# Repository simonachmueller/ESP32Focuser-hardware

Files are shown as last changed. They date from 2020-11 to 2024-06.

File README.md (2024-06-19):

# ESP32Focuser Hardware
This is a repository for storing documentation for my [ESP32Focuser](https://github.com/simonachmueller/ESP32Focuser) project.

Описание на русском

Deutsche Beschreibung

# What is that about
Focuser for astronomy telescope based on ESP32 controller. Comportable with Indilib (http:/indilib.org/) and ASCOM (https://ascom-standards.org/).
The controller uses the protocol Moonlite (as documented in the indilib project).

# What hardware do I need
The firmware runs on a [ESP32-DevKitC](https://www.espressif.com/en/products/devkits/esp32-devkitc/overview) board. It uses also the [BIGTREETECH TMC2209 V1.2 Stepper Motor Driver](https://github.com/bigtreetech/BIGTREETECH-TMC2209-V1.2) to drive the motor on a super-silent and vibrationless way. Basically, you only need this two boards to start using the focuser. If you want to build it on a more resilient way, you can follow intructions below.

# Schematics
Schematics diagram can be found as a KiCad project [folder](/schematics). You can donwload shematics as pdf [here](/schematics/ESP32Focuser.sch.pdf).

The schematics is pretty easy. You just connect the pins of the ESP32 dev board with the TMC2209 board, add power supply and connect motor - from this point you can control the focuser from the computer over ASCOM/INDI driver. If you want to use an optical encoder as a handcontroller (what I would really advise you if you want to get rid of vibrations when you touch the telescope focuser knob), connect it to the pins on the ESP32 board as well.

## Wiring table
Please use the wiring table as reference, it might get outdated. For the most latest schematics version, check the KiCad project.

| Description | ESP32 board | TMC2209 board | Note |
| --- | --- | --- | ---- |
| DIR | 32 | DIR | |
| STEP | 33 | STEP | |
| CLK | 25 | CLK | |
| PDN | 26 | PDN + PDN | not used |
| MS2 | 14 | MS2 | |
| MS1 | 12 | MS1 | |
| EN | 13 | EN | |
| ENC1 | 2 | | Encoder output 1 |
| ENC2 | 15 | | Encoder output 2 |
| 5V | 5V | VDD | |
| 12V | | VM | Motor power supply |

## Stepper motor
I use the 17HS2408 stepper motor, as it fits well for 12v supply: it has 8 Ohm phase resistance what leads to 1.5 Amps phase current, it's a bit over the specification (rated current 0.6 Amps) but as it's not supposed to continuously work on high speed in this project,it works just fine, has enough torque and does smooth movements. 

## BOM
Aka bill of material

| Description | AliExpress link |  Notes |
| --- | --- | --- |
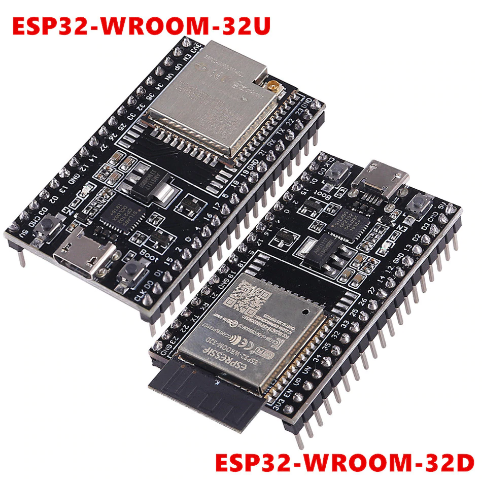
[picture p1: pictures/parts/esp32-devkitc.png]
| ESP32-DevKitC | https://www.aliexpress.com/item/4000103411061.html |  |
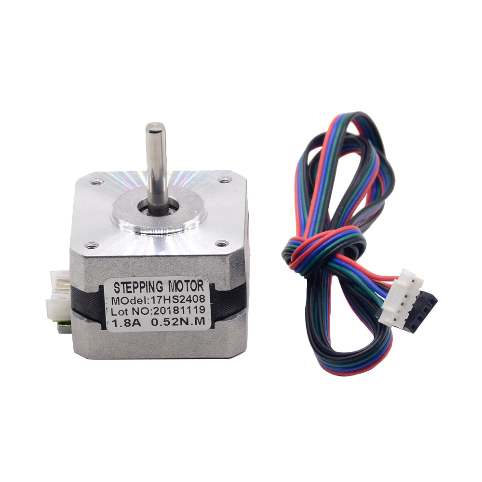
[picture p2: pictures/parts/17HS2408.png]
| 17HS2408 stepper motor | https://www.aliexpress.com/item/33033986185.html |  |
| 7 M3 screws for motor and encoder  | https://www.aliexpress.com/item/32965979997.html | M3 50pcs + 5mm  |
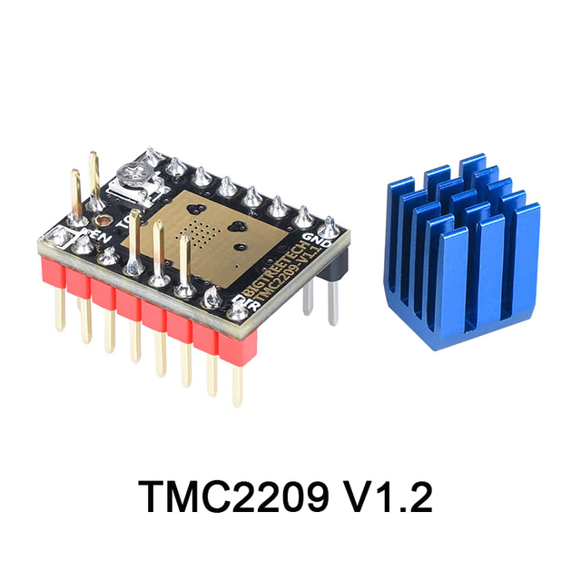
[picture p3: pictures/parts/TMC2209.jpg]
| TMC2209 board | https://www.aliexpress.com/item/33029587820.html |  |
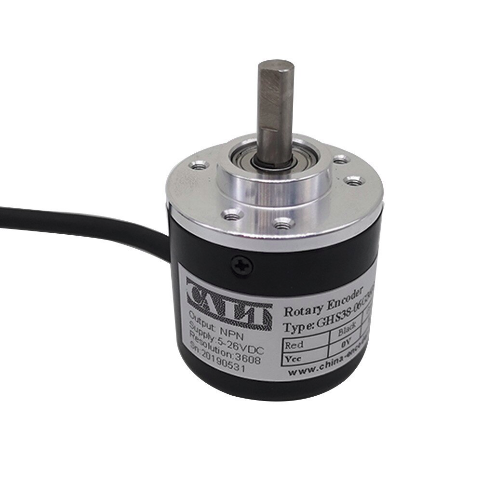
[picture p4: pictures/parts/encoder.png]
| Optical rotary encoder CALT ES38 | https://www.aliexpress.com/item/33028641351.html | 5v 600ppr  |
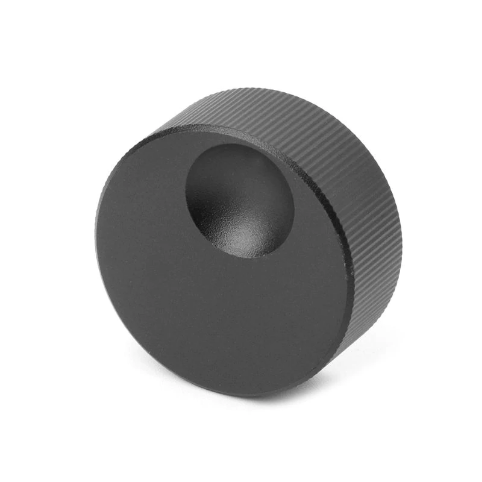
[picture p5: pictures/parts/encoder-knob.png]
| 13x32mm Encoder knob | https://www.aliexpress.com/item/33039964137.html | |
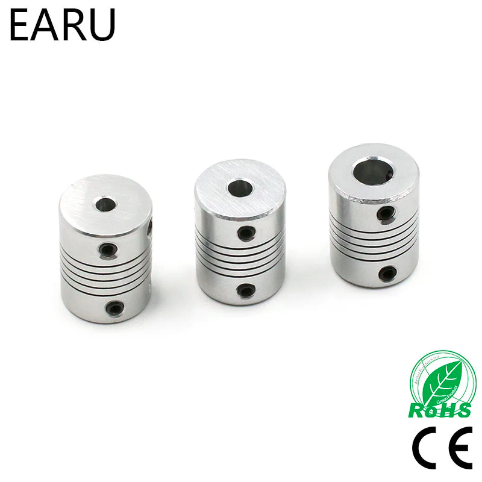
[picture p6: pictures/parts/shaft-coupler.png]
| Motor shaft coupler 5mm x ?? mm| https://www.aliexpress.com/item/32913158582.html ||
| OR alternatively to the direct coupling your motor with the focuser, you could use a belt like this below|||
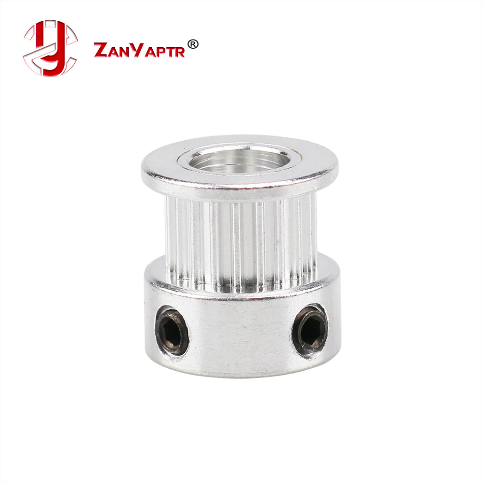
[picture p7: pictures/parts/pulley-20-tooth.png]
| GT2 Pulley 20 tooth ø 5mm| https://www.aliexpress.com/item/32724156349.html ||
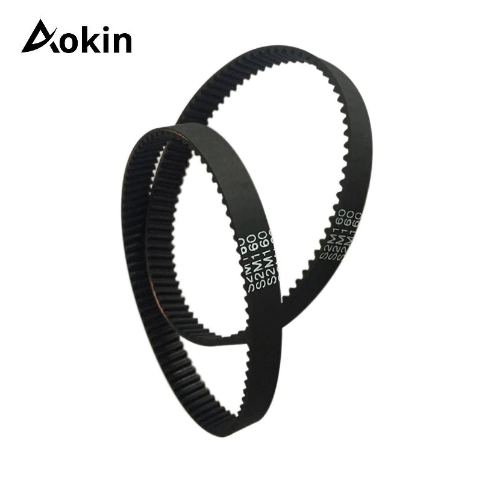
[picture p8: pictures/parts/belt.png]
| GT2 Closed Loop Timing Belt | https://www.aliexpress.com/item/32950422029.html ||
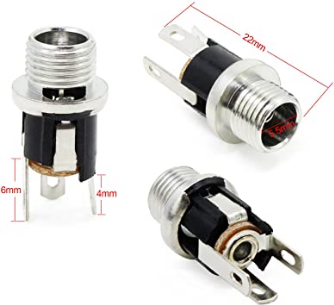
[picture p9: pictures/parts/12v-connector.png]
| 12v female plug 5.5mm x 2.1mm | |  |
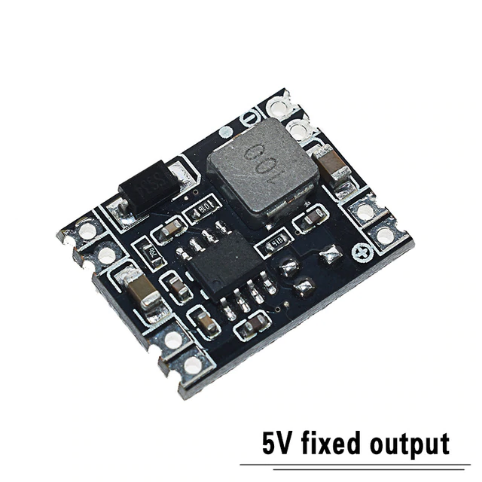
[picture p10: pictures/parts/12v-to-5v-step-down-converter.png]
| 12v→5v DC-DC step down converter board| https://www.aliexpress.com/item/32742116421.html ||
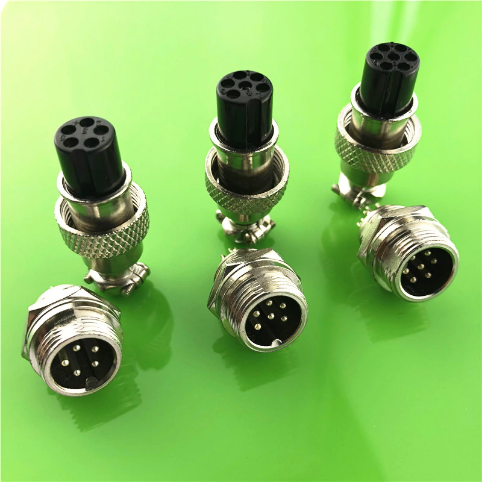
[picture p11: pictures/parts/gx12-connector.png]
| Hand controller connector M GX12 5 pin for encoder | https://www.aliexpress.com/item/32869491577.html | |
| Hand controller connector M GX12 4 pin for motor | https://www.aliexpress.com/item/32869491577.html | |
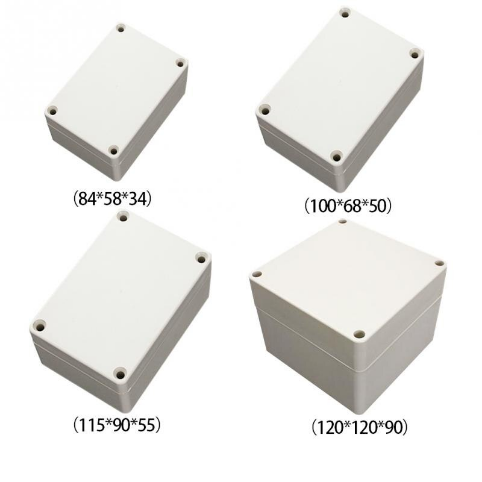
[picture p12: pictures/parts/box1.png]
| 115 90 55mm plastic enclosure case | https://www.aliexpress.com/item/32709832386.html |  |
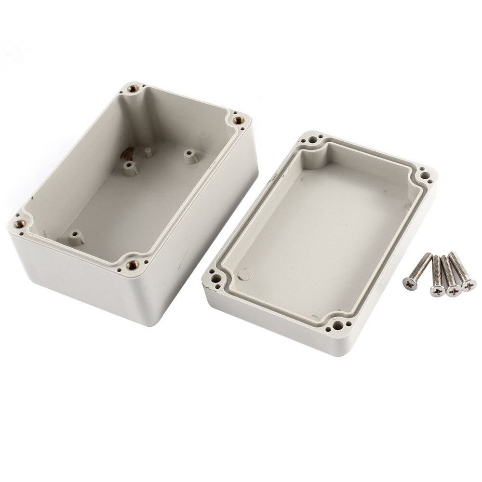
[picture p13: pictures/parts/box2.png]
| 100x68x50mm plastic enclosure case for encoder | https://www.aliexpress.com/item/32792270384.html | |
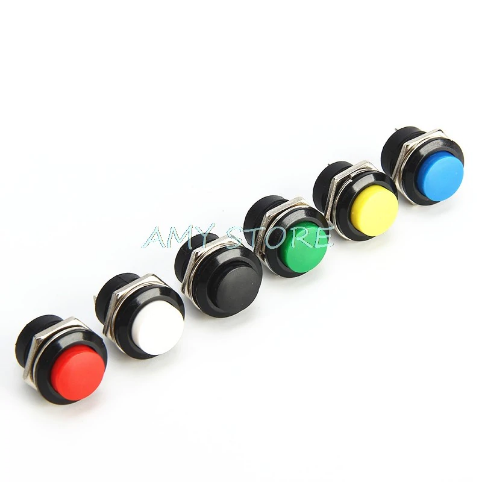
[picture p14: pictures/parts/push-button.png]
| Push button for handcontroller | https://www.aliexpress.com/item/32965284265.html ||
| Micro USB cable | tbd | |
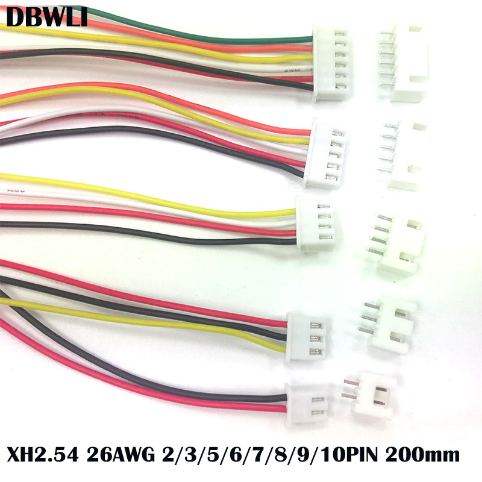
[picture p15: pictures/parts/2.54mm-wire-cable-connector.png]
| 2.54mm Wire Cable Connector 4 pin | https://www.aliexpress.com/item/32954418743.html | |
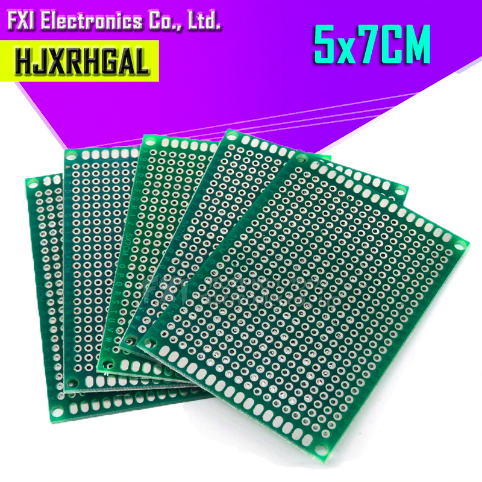
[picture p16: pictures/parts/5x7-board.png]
| Prototyping board 5x7 cm | https://www.aliexpress.com/item/32853911495.html |  |
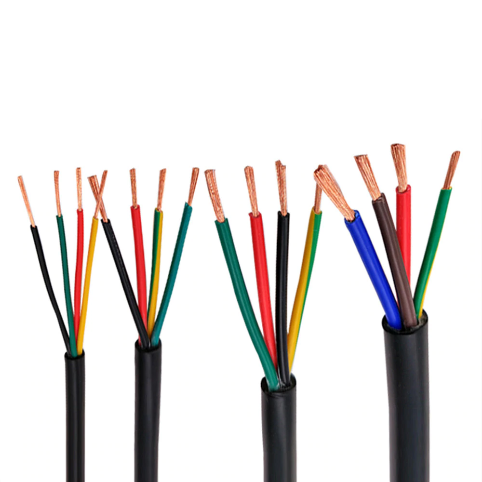
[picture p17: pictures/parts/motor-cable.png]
| Cable for motor 4 cores 0.3mm 22awg | https://www.aliexpress.com/item/4000714461664.html | |

# Pictures

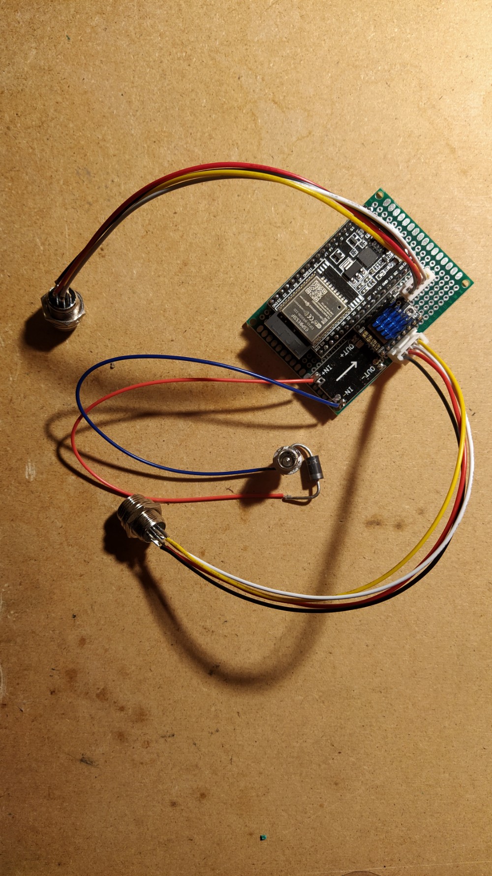
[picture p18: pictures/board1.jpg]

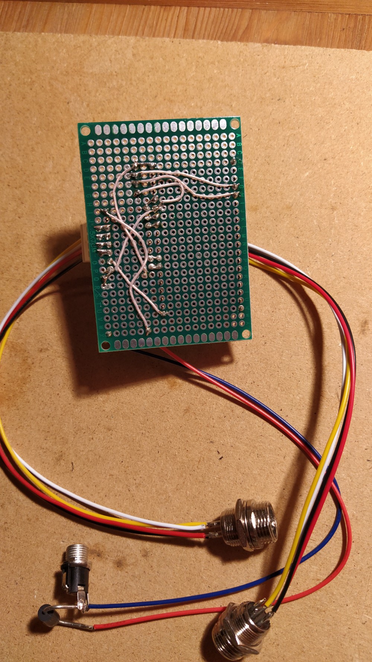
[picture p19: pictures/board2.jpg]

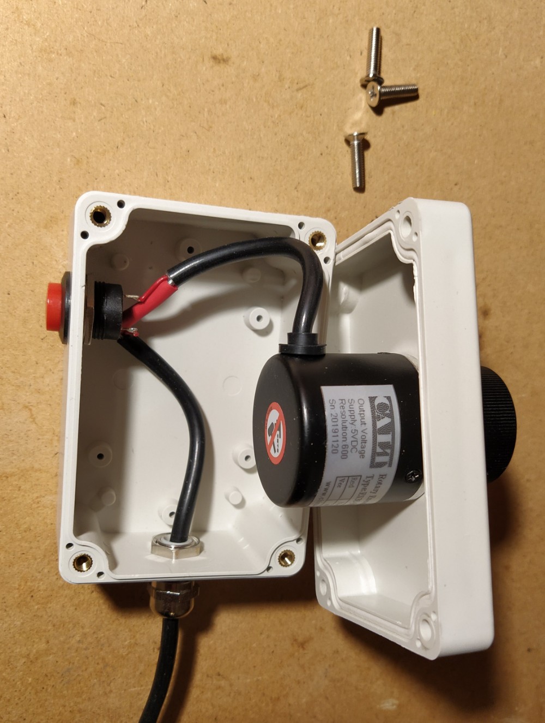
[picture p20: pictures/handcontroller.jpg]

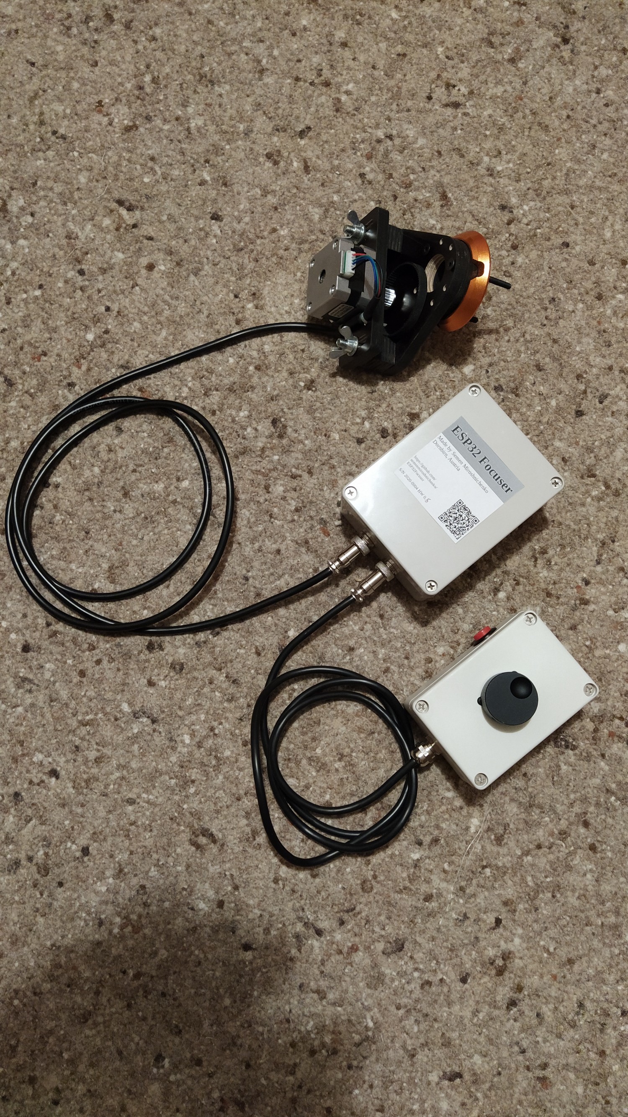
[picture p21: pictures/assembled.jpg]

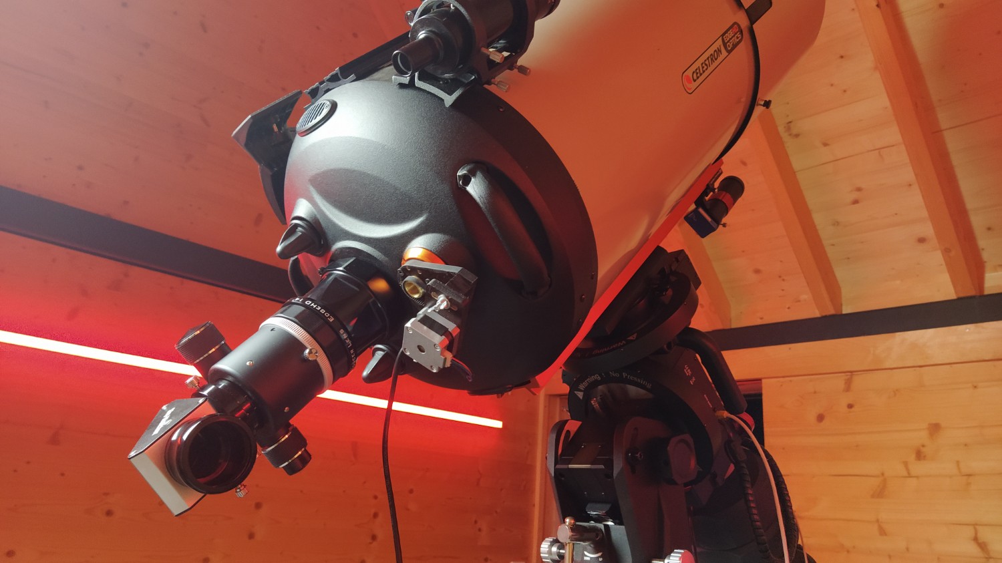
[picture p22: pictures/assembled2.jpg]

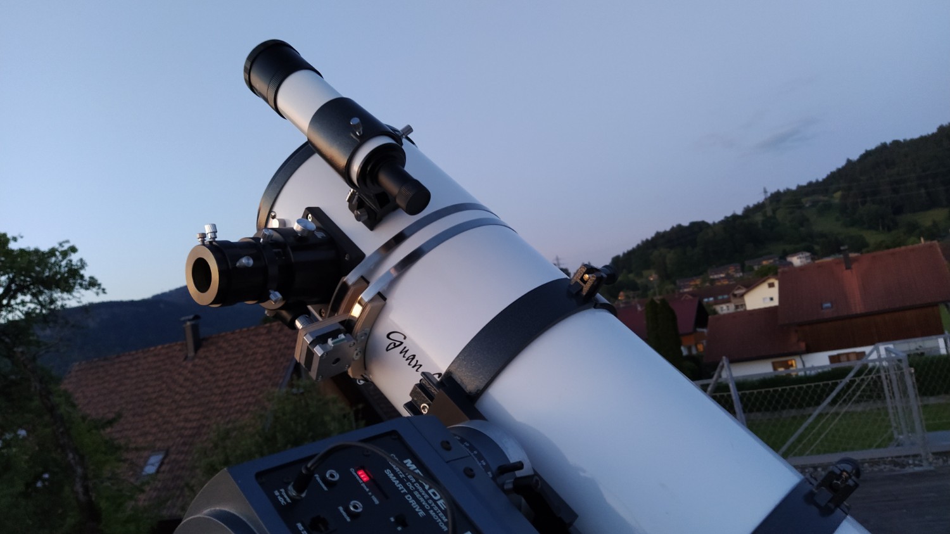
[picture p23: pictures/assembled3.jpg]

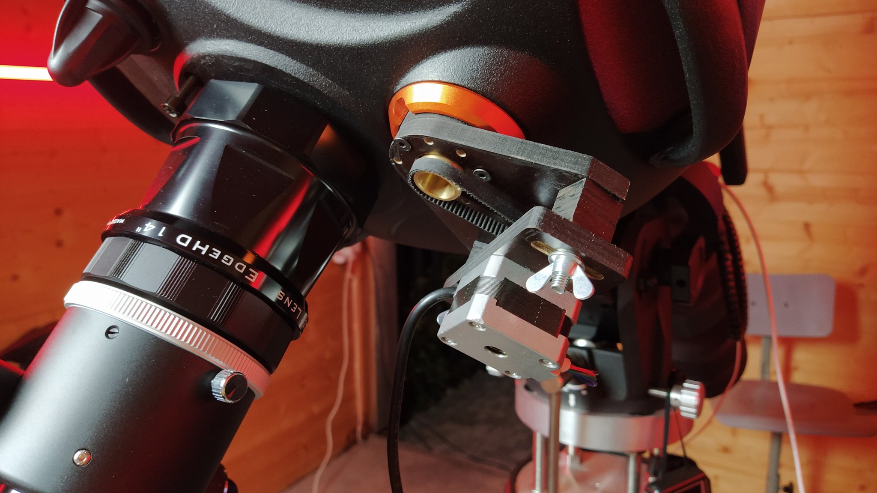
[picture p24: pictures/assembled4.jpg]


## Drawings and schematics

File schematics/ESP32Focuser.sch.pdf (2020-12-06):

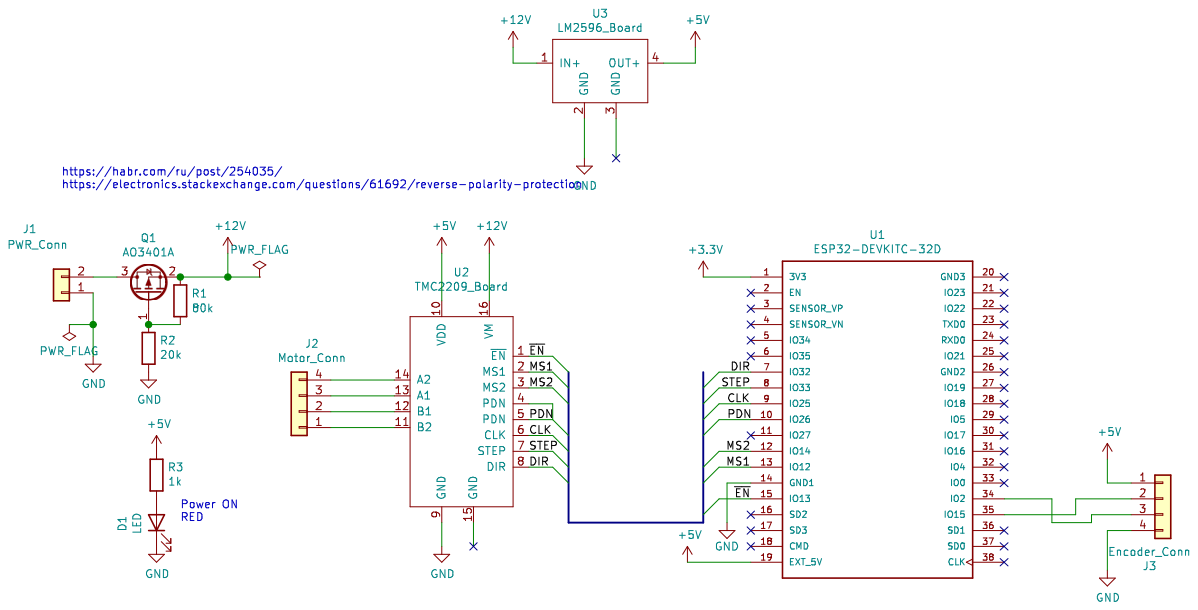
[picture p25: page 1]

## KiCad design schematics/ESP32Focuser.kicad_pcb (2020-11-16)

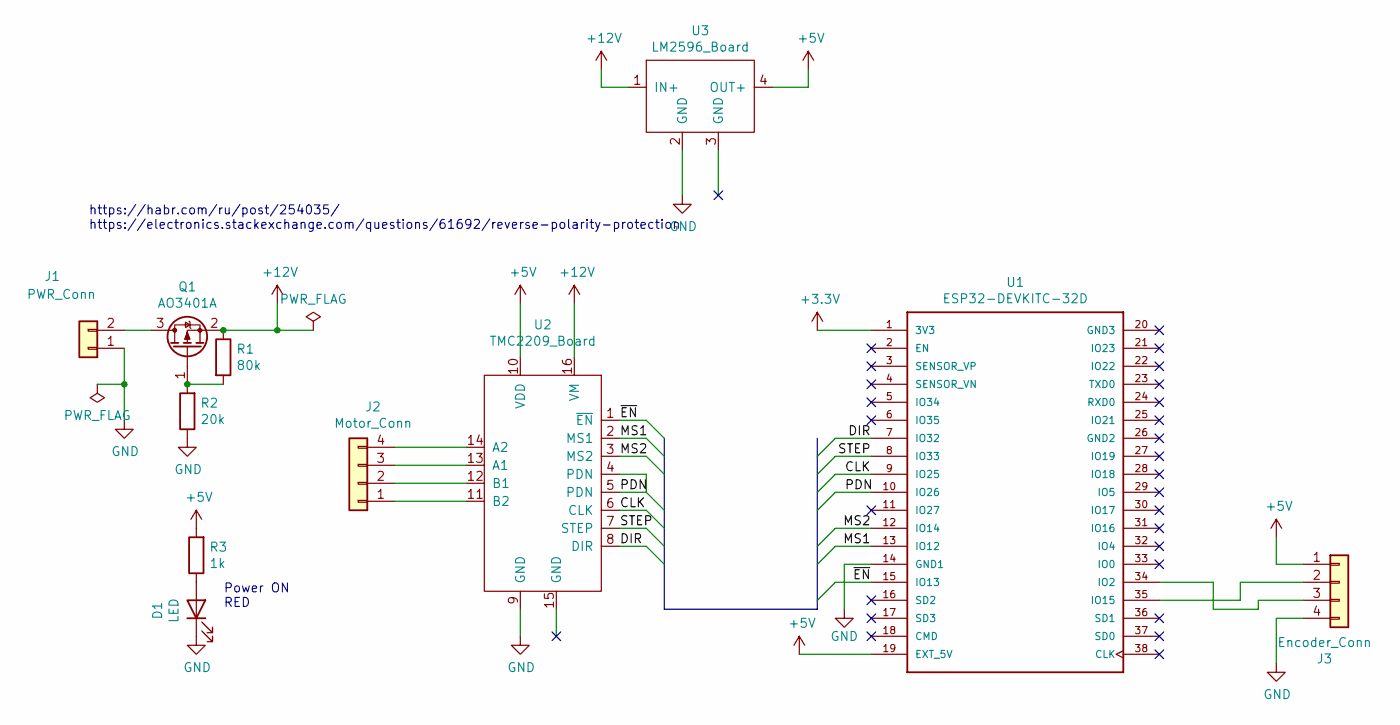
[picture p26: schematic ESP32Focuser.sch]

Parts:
D1: LED; LED_D3.0mm
J1: PWR_Conn; PinSocket_1x02_P2.54mm_Vertical
J2: Motor_Conn; PinSocket_1x04_P2.54mm_Vertical
J3: Encoder_Conn; PinSocket_1x04_P2.54mm_Vertical
Q1: AO3401A; SOT-23
R1: 80k; R_0805_2012Metric_Pad1.15x1.40mm_HandSolder
R2: 20k; R_0805_2012Metric_Pad1.15x1.40mm_HandSolder
R3: 1k; R_0805_2012Metric_Pad1.15x1.40mm_HandSolder
U1: ESP32-DEVKITC-32D; MODULE_ESP32-DEVKITC-32D
U2: TMC2209_Board; TMC2209_Module
U3: LM2596_Board; LM2596_Module

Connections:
+3V3: U1.1 (3V3)
+5V: J3.1, R3.2, U1.19 (EXT_5V), U2.10 (VDD), U3.4 (OUT+)
+12V: Q1.2 (S), R1.1, U2.16 (VM), U3.1 (IN+)
/CLK: U1.9 (IO25), U2.6 (CLK)
/DIR: U1.7 (IO32), U2.8 (DIR)
/MS1: U1.13 (IO12), U2.2 (MS1)
/MS2: U1.12 (IO14), U2.3 (MS2)
/PDN: U1.10 (IO26), U2.4 (PDN), U2.5 (PDN)
/STEP: U1.8 (IO33), U2.7 (STEP)
/~EN: U1.15 (IO13), U2.1 (~EN)
GND: D1.1 (K), J1.1, J3.4, R2.1, U1.14 (GND1), U2.9 (GND), U3.2 (GND)
unnamed: D1.2 (A), R3.1
unnamed: J1.2, Q1.3 (D)
unnamed: J2.1, U2.11 (B2)
unnamed: J2.2, U2.12 (B1)
unnamed: J2.3, U2.13 (A1)
unnamed: J2.4, U2.14 (A2)
unnamed: J3.2, U1.35 (IO15)
unnamed: J3.3, U1.34 (IO2)
unnamed: Q1.1 (G), R1.2, R2.2

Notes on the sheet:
https://habr.com/ru/post/254035/ https://electronics.stackexchange.com/questions/61692/reverse-polarity-protection
Power ON RED

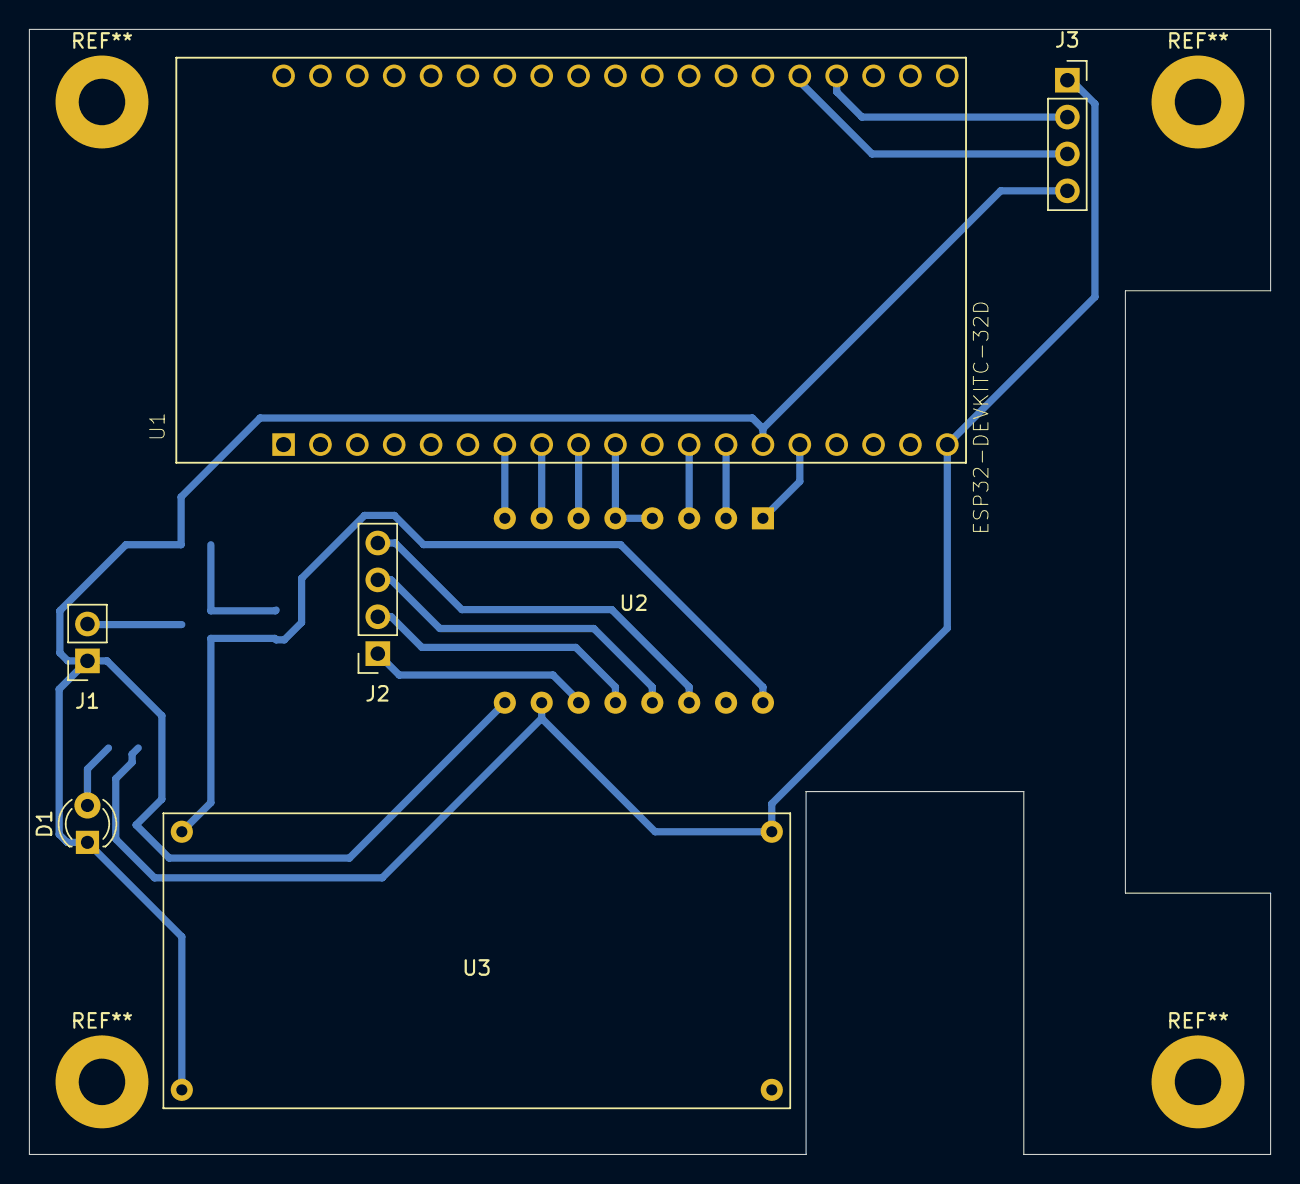
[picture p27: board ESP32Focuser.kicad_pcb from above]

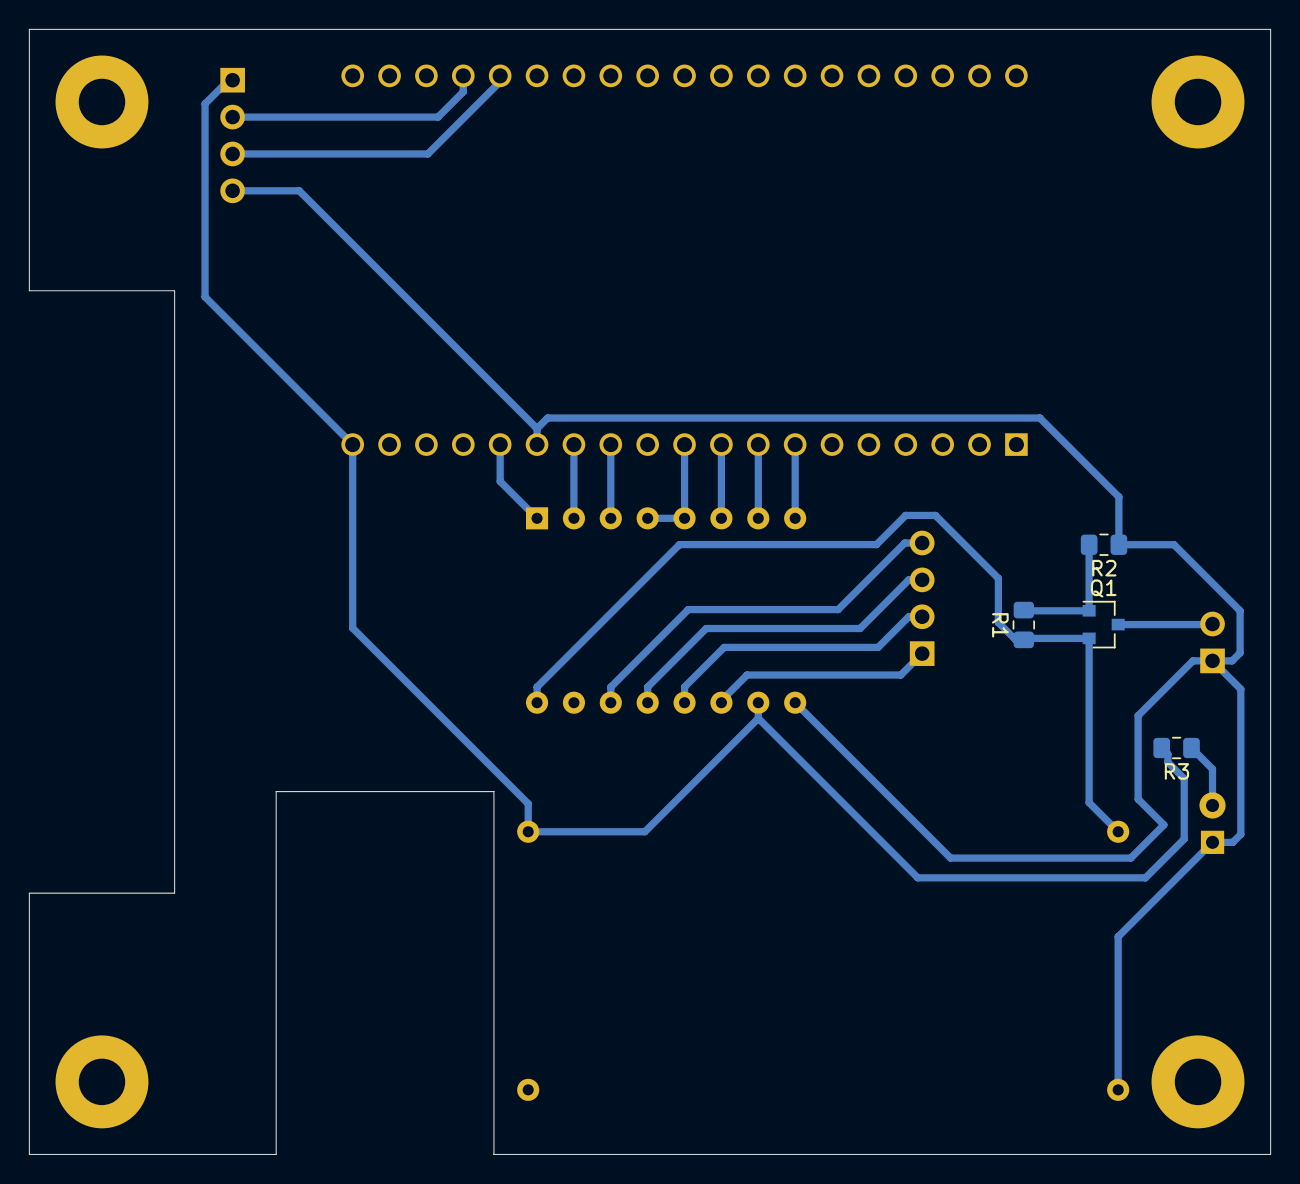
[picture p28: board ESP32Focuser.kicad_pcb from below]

Board: 2 copper layers, 85.5 x 77.5 mm, 11 parts (4 on the bottom side), 19 nets.

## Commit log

2020-11-16 Initial commit, KiCad project, pictures
    [ESP32Focuser.kicad_pcb, ESP32Focuser.sch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]
2020-11-16 Add motor information
2020-11-17 Add bill of material
2020-11-17 Add stepper motor picture
2020-11-17 Add optical encoder
2020-11-17 Add prototyping board and wire connector
2020-11-17 Add motor cable
2020-11-28 Add information about the timing belt option
2020-12-06 Add schematics as pdf
2020-12-06 Add link to schematics
